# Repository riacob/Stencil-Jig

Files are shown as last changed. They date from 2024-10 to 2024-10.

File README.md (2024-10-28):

# Stencil-Jig-Mod

## Improvements by riacob

- More printed parts, less hardware, for a cheaper build
- Convert bearing fittings to 608zz type
- TODO Add cylindrical spacer for 608zz bearings to adapt to screws
- Add [printable extrusion corners]((https://www.printables.com/model/181097-corner-brackets-for-system20-2020-2040-extrusion))
- Add [printable feet](https://www.printables.com/model/196231-kossel-2020-foot) 
- Add [printable extrusion caps](https://www.printables.com/model/146744-2020-extrusion-cap-5mm-slot)
- TODO Add printable jaws 
- Add assembly video link
- TODO Convert alignment guides to latching type
- TODO Magnetic pcb holders

## Details

The Stencil-Jig is a simple DIY machine for PCB stenciling built with the Openbuilds v-slot system. Dealing with those stencils is always tricky, because they have to be aligned perfectly to get great soldering results. So far, I was always using these stencils with spare PCBs around the project PCB which are fixed in position with tape. As I am using these stencils quite often in the last time I was thinking about creating a simple jig for it - and here it is.

The stencils can be clamped into the Stencil-Jig with the inner v-slot extrusions. With all the adjustment screws on the sides and the front, the PCB and the stencil can be aligned easily to fit each other (at least this is the plan). The PCB holders are not yet the best option but they are working for now. If you have other ideas of how the PCB alignment could be done better then please let me know!

These built is inspired by two other DIY designs of Stencil printers/jigs/machines:

- Valera Perinski: https://www.thingiverse.com/thing:3429201
- Dengler Mechatronik: https://dengler-mechatronik.de/?p=560

## Assembling

- [Creator's video](https://www.youtube.com/watch?app=desktop&v=ioedhoP2OJQ)

## Extrusions

V-slot extrusions are probably not necessary here, because the v-bearings are not used. Nevertheless I have chosen them because of the availability and v-style of the slots in order to align 3D-printed parts with only one screw.

For this project you will need 5x 500mm 2020 extrusions which will be cut into these dimensions:

- 6x 250mm; width of the jig (it is probably 249,5mm, because I have just cut a 500mm extrusion in half)
- 2x 500mm; length of the jig (can be shortened later, so I leaved it as it is first)

## What to print

For the complete machine, as it is seen in the picture below, you'll need the following parts to be printed:

- 1x hinge_left.stl
- 1x hinge_right.stl
- 4x slide_mount.stl
- 4x slider.stl
- 2x slide_stopper.stl
- 2x alignment_guide.stl
- 1x screwstop_m4_incl.stl
- 1x screwstop_m4_knob.stl
- 1x knob_m4.stl
- 4x screwstop.stl
- 4x knob_m3.stl
- 1x pcb_mount_edge_1_6mm.stl
- 1x pcb_mount_straight_1_6mm.stl
- 4x 2020_corner.stl
- 4x 2020_foot.stl 
- 4x 2020_cap.stl
- TODO 2x 5_20_220_jaws.stl

## What you need

Except the 3D printed parts and the extrusions listed above you will also need the following parts:\
PARTS IN RED CAN ALSO BE PRINTED

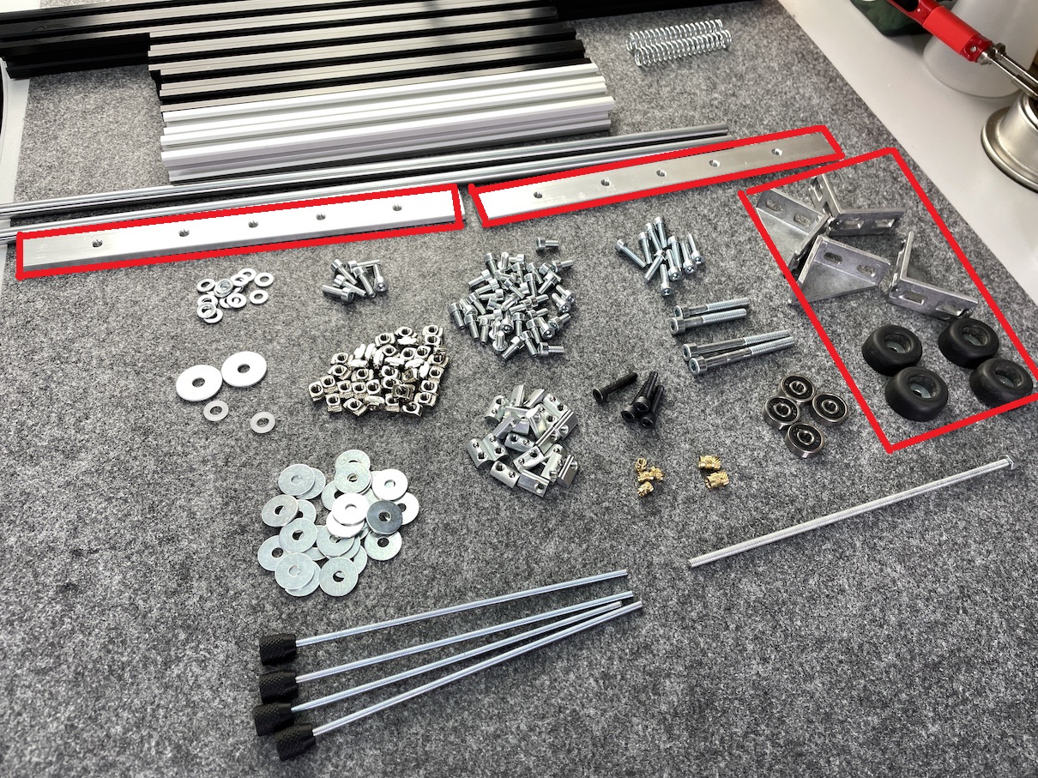
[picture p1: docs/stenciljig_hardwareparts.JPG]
</a>

- 2x 8mm stainless steel rod (length = length of the jig - 40mm)
- 4x 608ZZ bearings
- 2x Strong springs for the 8mm rod
- 4x M3 threaded rod ~100mm
- 1x M4 threaded rod ~100mm
- 1x Steel plate 1mm (~290mmx250mm)
- 4x M3 threaded insert
- 3x M4 threaded insert
- 40x M4 screw DIN 912 8mm
- 10x M4 screw DIN 912 12mm
- 10x M4 screw DIN 912 20mm
- 4x M4 screw DIN 912 25mm
- 2x M5 screw DIN 912 50mm
- 2x M5 screw DIN 912 30mm
- 64x M4 extrusion nuts
- 1x M4 self-locking nut
- 20x Metal washers 4,3mm x 15mm
- 4x Metal washers 5,3mm x 15mm
- 2x Nylon washers 5,3mm x 10mm
- TODO 2x Rubber sheet for jaws LxHxW
- 4x Felt or rubber pads for the feet

## Alignment guides

</a>

The alignment guides are there to hold the upper part of the jig (including the stencil) during the stenceling process in place, so that it doesn't move to the left or right.

## Gallery

</a>
</a>
</a>

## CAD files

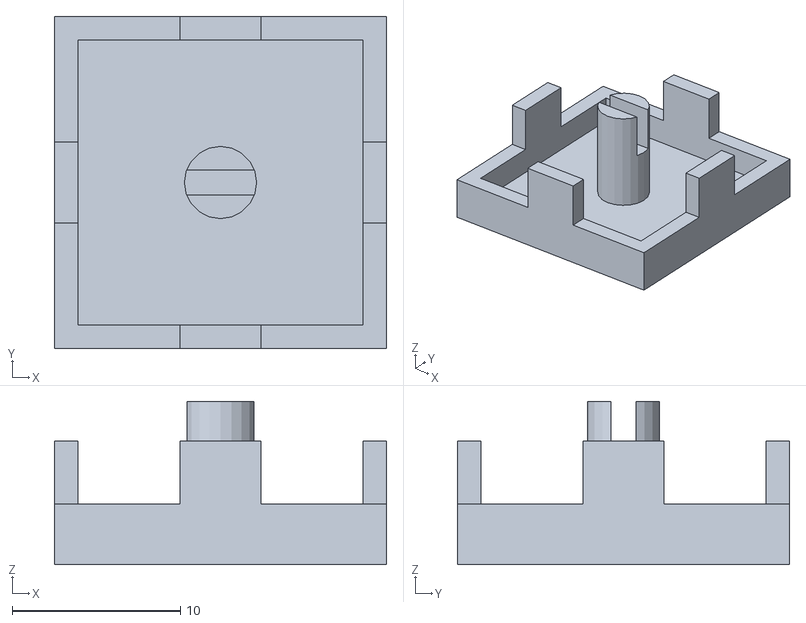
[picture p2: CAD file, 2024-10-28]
3d_files/2020_cap.stl
19.8 x 19.8 x 9.70

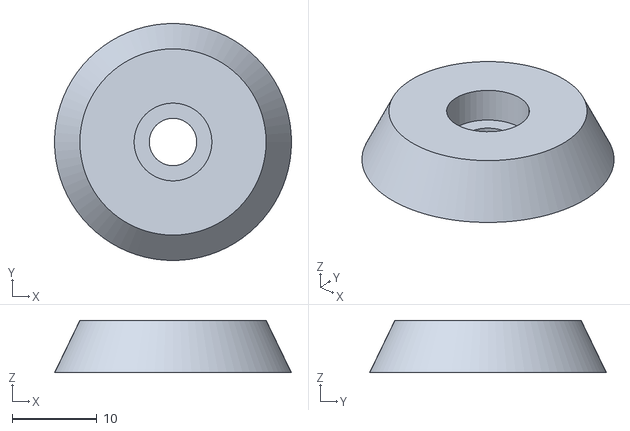
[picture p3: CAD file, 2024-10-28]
3d_files/2020_foot.stl
28.0 x 28.0 x 6.20

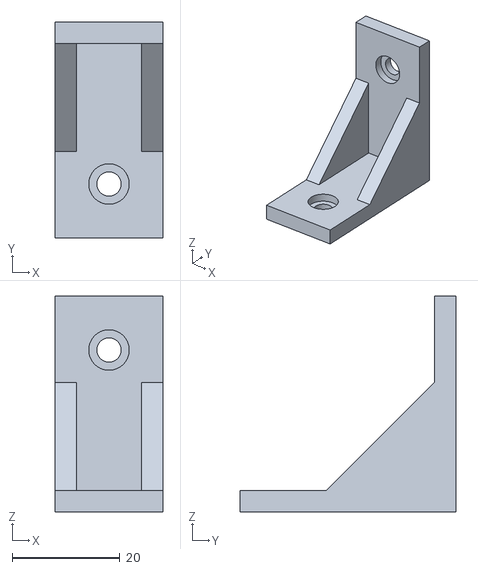
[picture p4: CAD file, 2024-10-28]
3d_files/2020_corner.stl
20.0 x 40.0 x 40.0

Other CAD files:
3d_files/StencilJig_608zz.f3z
